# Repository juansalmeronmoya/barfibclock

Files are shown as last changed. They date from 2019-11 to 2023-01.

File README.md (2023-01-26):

IMG_20200908_175020_Bokeh

# BarFIBclock
Repository used to share my work for the clock installed on the [Facultat d'Informàtica de Barcelona (FIB) bar](https://goo.gl/maps/2sY8hWTRuadKxtpD8)

## Materials
 - 28 x 9g Servo [link](https://s.click.aliexpress.com/e/_ABv179)
 - 1 x Arduino Pro mini Atmega328 [link](http://bit.ly/2NVvFll)
 - 2 x I2C PCA9685 servo controller [link](https://s.click.aliexpress.com/e/_AAJpyf)
 - 1 x DC 5V3A adapter [link](http://bit.ly/2NvYGVG)
 - 1 x DC connector [link](http://bit.ly/33AKoJ4)
 - 1 x DS3231 RTC module [link](http://bit.ly/32uphGY)
 - 1 x CR2032 3v battery [link](http://bit.ly/2PYQaAa)
 - 3 x 12mm Metal Push Button Switch Momentary High [link](https://bit.ly/337vpaj)
 - 20 x 150~300mm Servo Extension Lead Wire Cable [link](https://bit.ly/3iaA7dB)
 - 1 x Breadboard Jumper Cable Wires Kit 6cm [link](https://bit.ly/2ZxfuBp)
 - 1 x Red/Black Cable 26AWG 150mm  [link](https://bit.ly/35eJe9F)
 - 12 x M2.5 Screws and nuts
 
### Extras
 - 1 x FTDI USB to TTL UART FT232 [link](https://bit.ly/2R5Vjpw)
 - Cable ties [link](https://s.click.aliexpress.com/e/_9ybz9t)
 - Cyanoacrylate Glue (Superglue like)
 - Heat-shrink tubing [link](https://s.click.aliexpress.com/e/_Aswi55)

## Printing 3D models



| Qty | Filename 
| --- | ---
| 4 | [dc_segment_a.stl](3dparts/frame_segments/dc_segment_a.stl) 
| 4 | [dc_segment_b.stl](3dparts/frame_segments/dc_segment_b.stl) 
| 4 | [dc_segment_c.stl](3dparts/frame_segments/dc_segment_c.stl) 
| 4 | [dc_segment_d.stl](3dparts/frame_segments/dc_segment_d.stl) 
| 4 | [dc_segment_e.stl](3dparts/frame_segments/dc_segment_e.stl) 
| 4 | [dc_segment_f.stl](3dparts/frame_segments/dc_segment_f.stl) 
| 4 | [dc_segment_g.stl](3dparts/frame_segments/dc_segment_g.stl) 
| 4 | [custom_base.stl](3dparts/frame_segments/custom_base.stl) 
| 1 | [dc_base_center.stl](3dparts/frame_segments/dc_base_center.stl) 
| 2 | [dc_frame_corner1.stl](3dparts/frame_segments/dc_frame_corner1.stl) 
| 2 | [dc_frame_corner2.stl](3dparts/frame_segments/dc_frame_corner1.stl) 
| 1 | [dc_frame_top.stl](3dparts/frame_segments/dc_frame_top.stl) 
| 1 | [dc_frame_bottom.stl](3dparts/frame_segments/dc_frame_bottom.stl) 
| 18  | [dc_washer.stl](3dparts/frame_segments/dc_washer.stl)
| 8 | [custom_shoe_ag.stl](3dparts/frame_segments/custom_shoe_ag.stl) 
| 8 | [custom_shoe_bf.stl](3dparts/frame_segments/custom_shoe_bf.stl) 
| 8 | [custom_shoe_ce.stl](3dparts/frame_segments/custom_shoe_ce.stl) 
| 4 | [custom_shoe_d.stl](3dparts/frame_segments/custom_shoe_d.stl)
| 2 | [dc_shoe_center.stl](3dparts/frame_segments/dc_shoe_center.stl)
| 1 | [custom_electronics_case_v2](3dparts/frame_segments/custom_electronics_case_v2.stl)

note: info extracted from http://www.otvinta.com/download14.html

## Electronics


IMG_20211107_132942_Bokeh

## How to program it

Using a USB FTDI controller you can flash the arduino pro mini using arduino IDE selecting this parameters:
* Board: "Arduino Pro or Pro mini"
* Processor: ATmega328P 5V
* Port: your USB FTDI serial port

The programmer is connected with this connection diagram:



## History and Maintenance Book

[Jan 2023] 
* Servos replacement (caused by +800k cycles operation wear) some were died other just as prevention.
* Flashed new servo operation limits

[Dec 2021] 
* Fixed segment movement order and timing to avoid segment collisions
* Upgraded to tighter segment shoes to avoid segment collisions
* Died servos replacement (caused by collisions)

[~2021]
* Died servos replacement (caused by collisions)
* Glued again some servos

[Sept 2020]
* Final hardware with top case and easy programming buttons and wiring
* Installation on the Bar FIB wall, Hurra!

[Dec 2019]
* Hardware and software development with arduino

## Previous work
This project is inspired and based on the otvinta3d clock.
Most of the 3D models used are the same, you can check them out at
https://www.thingiverse.com/thing:3266949

Arduino code are also inspired on the work of https://github.com/ardenpm/servo_clock and https://www.thingiverse.com/thing:3375870

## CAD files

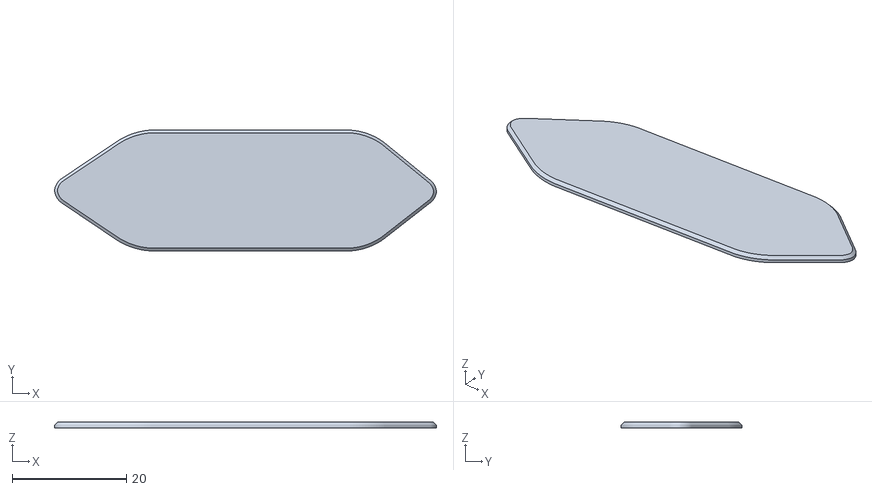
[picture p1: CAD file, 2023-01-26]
3dparts/frame_segments/custom_shoe_d_v2.stl
67.0 x 21.2 x 1.00

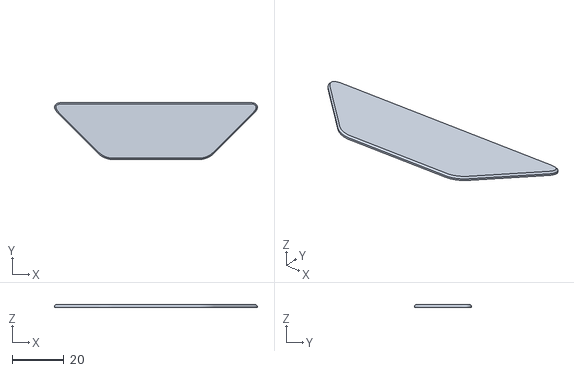
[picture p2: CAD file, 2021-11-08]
3dparts/frame_segments/custom_shoe_ag.stl
78.3 x 22.0 x 1.00

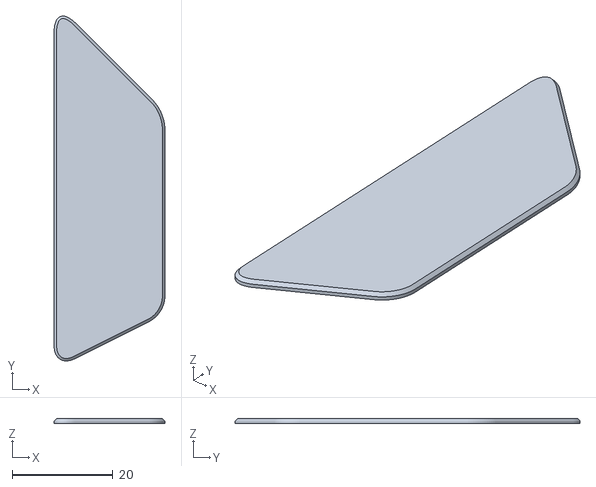
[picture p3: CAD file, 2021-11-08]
3dparts/frame_segments/custom_shoe_bf.stl
22.0 x 68.5 x 1.00

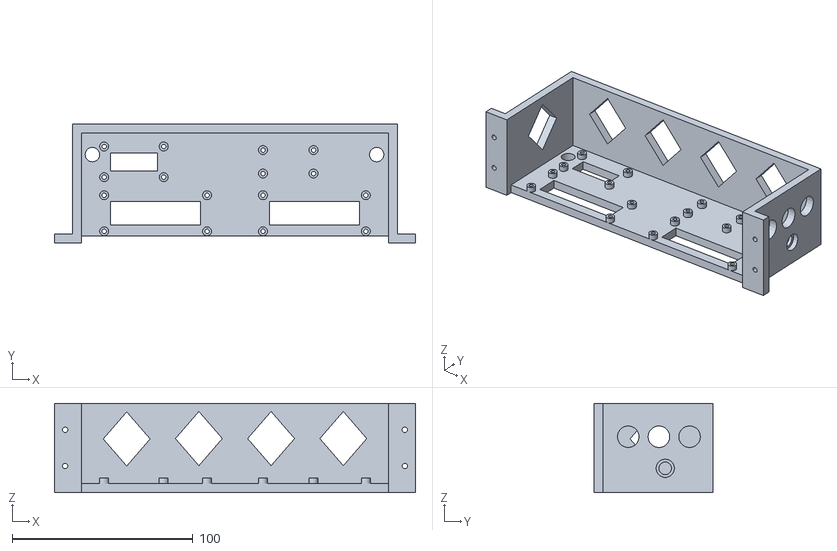
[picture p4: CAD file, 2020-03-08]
3dparts/frame_segments/custom_electronics_case_v2.stl
200.0 x 66.0 x 49.5

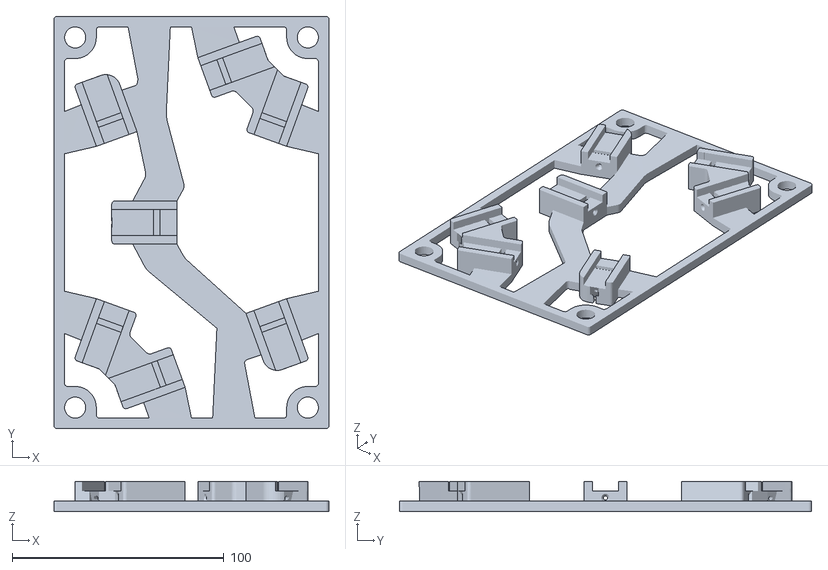
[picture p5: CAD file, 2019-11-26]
3dparts/frame_segments/custom_base.stl
130.0 x 195.0 x 14.3

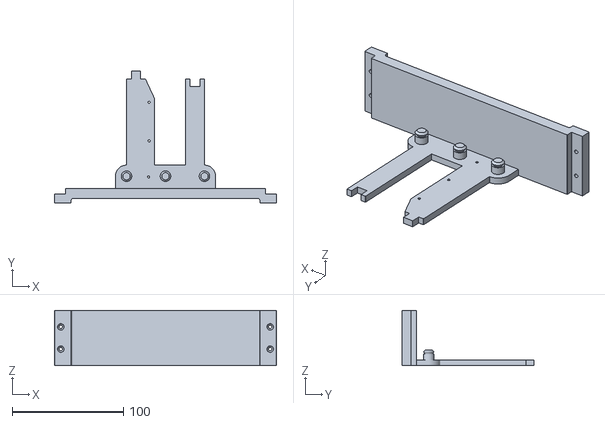
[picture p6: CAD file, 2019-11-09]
3dparts/frame_segments/dc_frame_bottom.stl
199.5 x 118.5 x 49.6

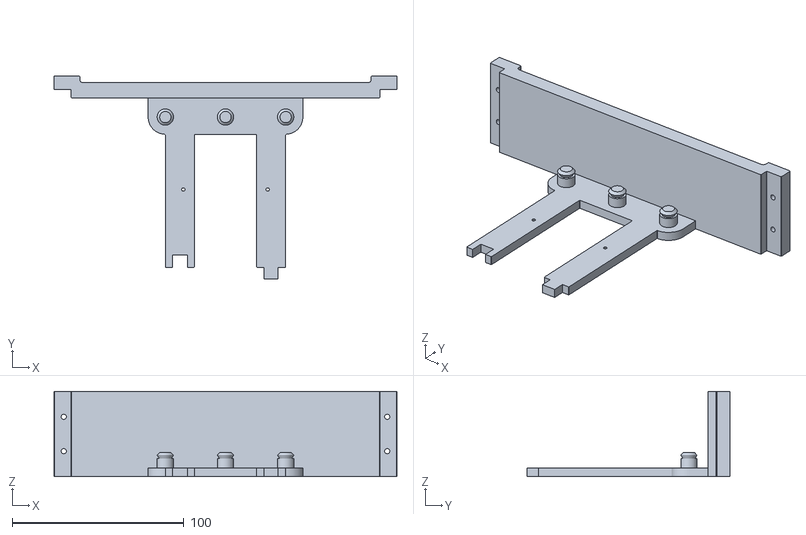
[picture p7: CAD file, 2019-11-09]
3dparts/frame_segments/dc_frame_top.stl
199.5 x 118.3 x 49.6

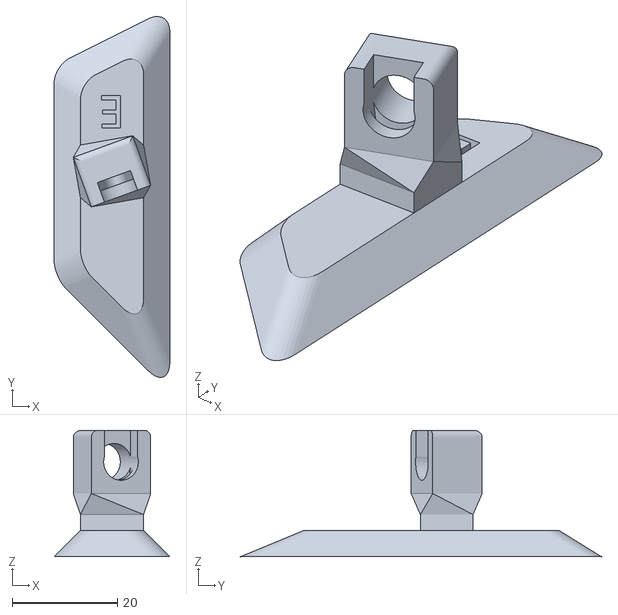
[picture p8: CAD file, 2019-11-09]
3dparts/frame_segments/dc_segment_e.stl
22.0 x 68.5 x 24.0

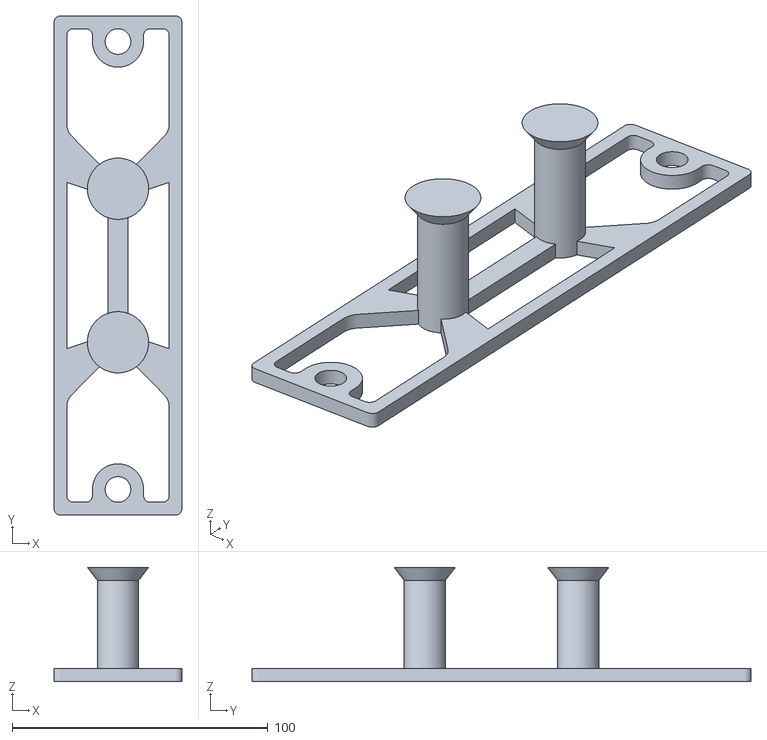
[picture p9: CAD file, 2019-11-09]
3dparts/frame_segments/dc_base_center.stl
50.0 x 195.0 x 44.6

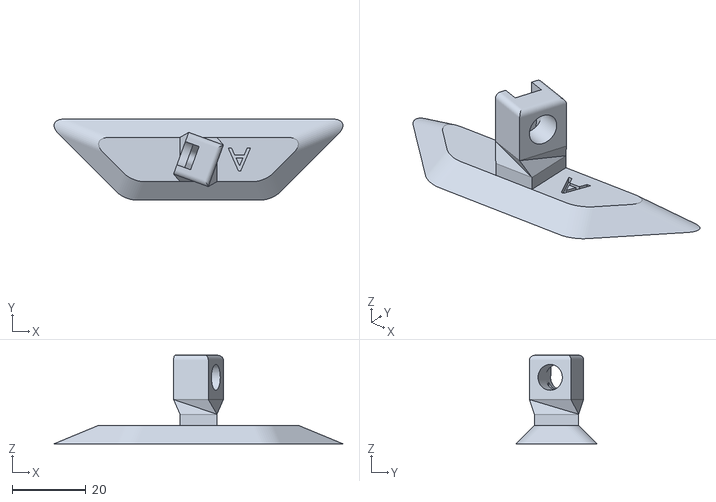
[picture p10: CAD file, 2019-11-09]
3dparts/frame_segments/dc_segment_a.stl
78.3 x 22.0 x 24.0

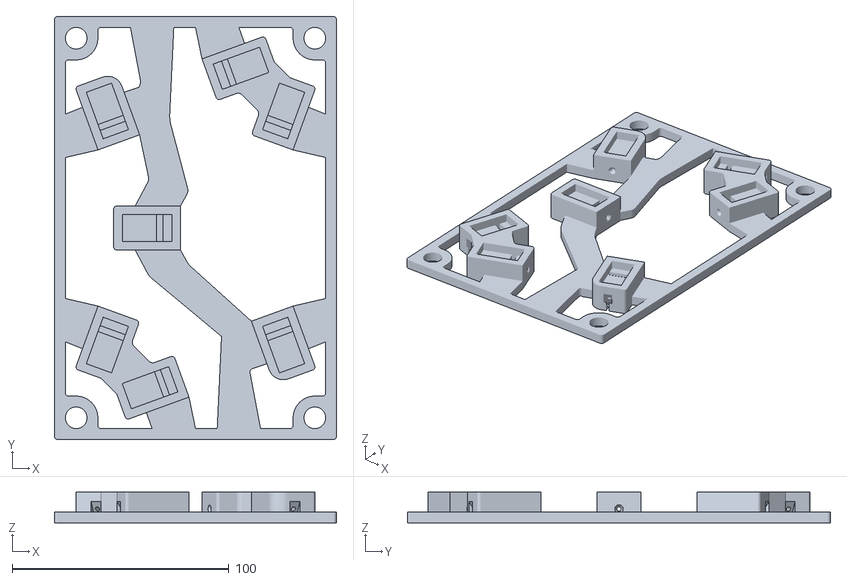
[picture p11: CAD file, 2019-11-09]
3dparts/frame_segments/dc_base.stl
130.0 x 195.0 x 14.3

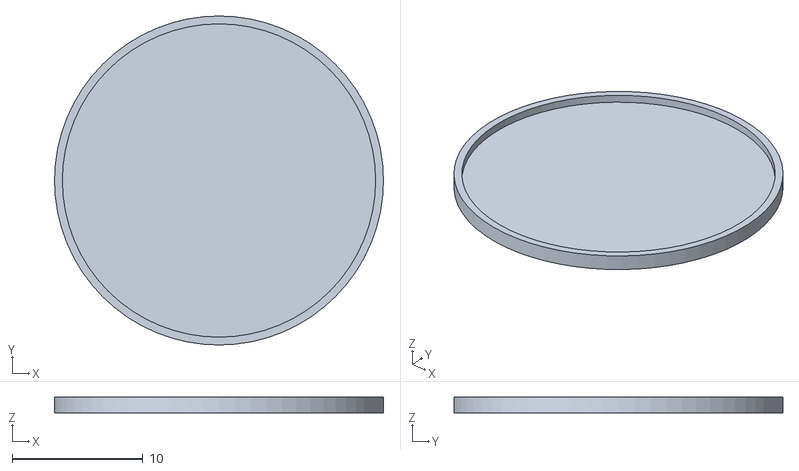
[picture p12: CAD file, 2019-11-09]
3dparts/frame_segments/dc_shoe_center.stl
25.1 x 25.1 x 1.20

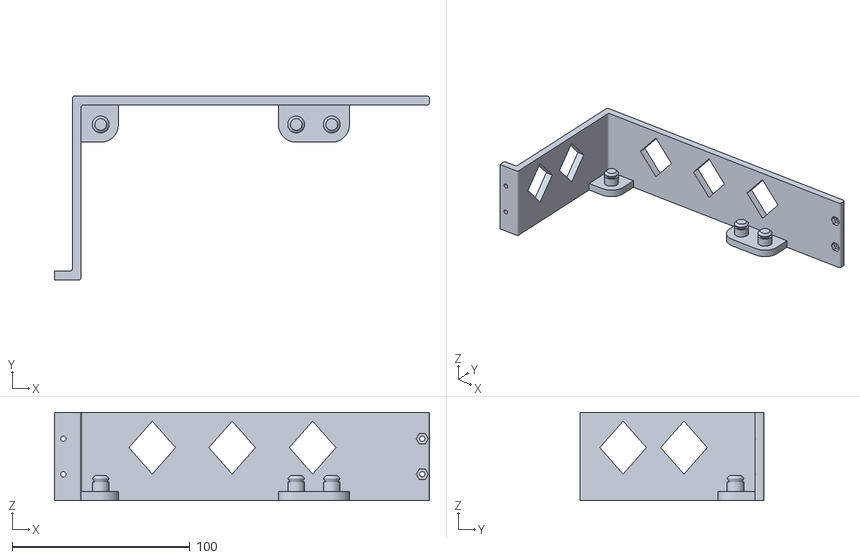
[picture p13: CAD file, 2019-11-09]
3dparts/frame_segments/dc_frame_corner1.stl
211.0 x 103.5 x 49.6

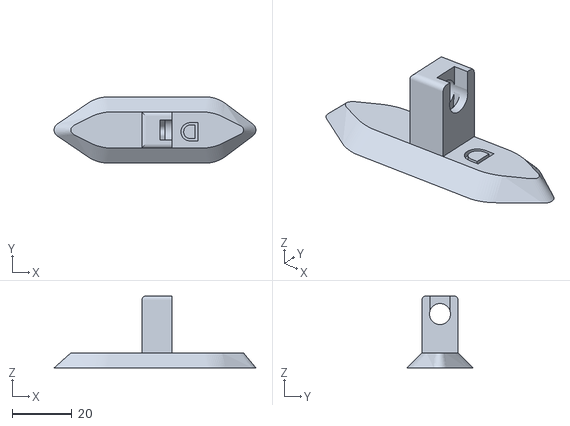
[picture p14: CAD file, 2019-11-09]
3dparts/frame_segments/dc_segment_d.stl
67.4 x 22.0 x 24.0

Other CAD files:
3dparts/frame_segments/custom_shoe_ce.stl
3dparts/frame_segments/dc_segment_c.stl
3dparts/frame_segments/dc_segment_b.stl
3dparts/frame_segments/dc_segment_g.stl
3dparts/frame_segments/custom_shoe_d.stl
3dparts/frame_segments/dc_frame_corner2.stl
3dparts/frame_segments/dc_segment_f.stl
3dparts/frame_segments/dc_washer.stl

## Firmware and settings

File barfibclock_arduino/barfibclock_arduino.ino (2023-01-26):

#include <Wire.h>
#include <Adafruit_PWMServoDriver.h> // PCA9685 library
#include <RTClib.h> //Real Time Clock library

Adafruit_PWMServoDriver servoHours = Adafruit_PWMServoDriver(0x40); //first PCA9685 address
Adafruit_PWMServoDriver servoMinutes = Adafruit_PWMServoDriver(0x41); //second PCA9685 address
RTC_DS3231 rtc; //RTC address

// reference LOW to power buttons
const int setmodelow_pin = 4;
const int setpluslow_pin = 6;
const int setminuslow_pin = 2;

// servo enable pin
const int enablepin = 12;

// read button pins
const int setmodepin = 5;
const int setpluspin = 7;
const int setminuspin = 3;

const byte mapchar [11][7] = { //for each number, position of every segment
  {1, 1, 1, 0, 1, 1, 1}, // zero - segment number from top lo low, left to right
  {0, 0, 1, 0, 0, 1, 0}, // one
  {1, 0, 1, 1, 1, 0, 1}, // two
  {1, 0, 1, 1, 0, 1, 1}, // three
  {0, 1, 1, 1, 0, 1, 0}, // four
  {1, 1, 0, 1, 0, 1, 1}, // five
  {1, 1, 0, 1, 1, 1, 1}, // six
  {1, 0, 1, 0, 0, 1, 0}, // seven
  {1, 1, 1, 1, 1, 1, 1}, // eight
  {1, 1, 1, 1, 0, 1, 1}, // nine
  {0, 0, 0, 0, 0, 0, 0} // null (all down)
};

const int servolow [4] [7] = { 
// pulse to add to servopulse for fine tunning of each individual servo
// higher numbers represents a servo position more clockwise if you look the servo from the cable side
  {400, 500, 130, 180, 280, 410, 330}, //digit 0. 
  {420, 330, 170, 180, 180, 400, 350}, //digit 1
  {400, 400, 210, 180, 270, 510, 380}, //digit 2
  {390, 420, 250, 210, 250, 460, 370}  //digit 3
};

const int servohigh [4] [7] = { 
// pulse to add to servopulse for fine tunning of each individual servo
// higher numbers represents a servo position more clockwise if you look the servo from the cable side
  {220, 300, 380, 410, 480, 170, 130}, //digit 0 
  {220, 130, 410, 400, 420, 130, 170}, //digit 1 
  {190, 180, 480, 400, 510, 270, 180}, //digit 2
  {200, 190, 450, 450, 440, 230, 170}  //digit 3
};

byte moment [4] = {8, 8, 8, 8}; // actual time
byte momentnull [4] = {10, 10, 10, 10}; // all digits in null for startup
byte momenthigh [4] = {8, 8, 8, 8}; // all digits in null for startup
byte momentdisplay [4]; //time shown in display

void setup() {

  Serial.begin(9600);
  rtc.begin();
  //rtc.adjust(DateTime(__DATE__, __TIME__)); //uncomment to set time to now
  //rtc.adjust(DateTime(2019, 12, 27, 22, 51, 0)); 
  pinMode(enablepin, OUTPUT); // this is the pin for OE in the PCA (enable/disable servos LOW/HIGH)
  pinMode(setmodelow_pin, OUTPUT);
  pinMode(setpluslow_pin, OUTPUT);
  pinMode(setminuslow_pin, OUTPUT);
  digitalWrite(setmodelow_pin, LOW);
  digitalWrite(setpluslow_pin, LOW);
  digitalWrite(setminuslow_pin, LOW);
  pinMode(setmodepin, INPUT_PULLUP); // this is the pin for set time button
  pinMode(setpluspin, INPUT_PULLUP); // this is the pin for set plus button
  pinMode(setminuspin, INPUT_PULLUP); // this is the pin for set minus button
  servoHours.begin();
  servoHours.setPWMFreq(50); // set frequncy for first PCA
  servoMinutes.begin();
  servoMinutes.setPWMFreq(50); // set frequency for second PCA
  showtime(moment, 0);
  showtime(momentnull, 50);
}

void loop() {
  //tuning();
  capturetime(); // captura el momento!
  showtime(moment, 20);
  while (momentdisplay[3] == moment[3]) { // wait while minutes doesnt change...
    if (digitalRead(setmodepin) != HIGH) setmode(momentdisplay);
    capturetime();
  }
}

void tuning() {
  byte servoToTune = 0;
  int pulseToTune = 0;
  
  while (!Serial) {
    ; // wait for serial port to connect. Needed for native USB
  }
  if (Serial.available() > 0) {
    Serial.println("Enter servo to tune");
    servoToTune = Serial.readString().toInt();

    Serial.print("Tuning servo #");
    Serial.println(servoToTune, DEC);
    

    while (pulseToTune != -1) {
      if (Serial.available() > 0) {
        Serial.println("Enter pulse to test, -1 for exit"); 
        pulseToTune = Serial.readString().toInt();
        
        Serial.print("Servo #");
        Serial.print(servoToTune, DEC);
        Serial.print(" value: ");
        Serial.println(pulseToTune, DEC);

        //move servo
        digitalWrite(enablepin, LOW);
        if(servoToTune >= 21) {
          servoMinutes.setPWM(servoToTune-13, 0, pulseToTune);
        } else if(servoToTune >= 14 && servoToTune < 21) {
          servoMinutes.setPWM(servoToTune-14, 0, pulseToTune);
        } else if(servoToTune >= 7 && servoToTune < 14) {
          servoHours.setPWM(servoToTune+1, 0, pulseToTune);
        } else{
          servoHours.setPWM(servoToTune, 0, pulseToTune);
        }
        delay(1000);
        digitalWrite(enablepin, HIGH);
      }
    }
    pulseToTune = 0;
  }
}

void capturetime() {
  DateTime now = rtc.now(); // save in variable now the actual time;
  moment[0] = now.hour() / 10; // find out first digit from hour
  moment[1] = now.hour() - moment[0] * 10; // find out second digit from hour
  moment[2] = now.minute() / 10; // find our first digit from minute
  moment[3] = now.minute() - moment[2] * 10; // find out second digit from minute
}

void showtime(byte m [4], int w) {
  int d = 1200; // delay needed to stop the servos moving before disabling them
  // parameters: matrix with the digits to show
  if (memcmp(m, momentdisplay, 4) != 0) { // if time displayed is different to time expected to be shown
    digitalWrite(enablepin, LOW); // enable the servos
    for (int i = 0; i < 4; i++) { // for every single position, show only if different to actually shown
      if (m[i] != momentdisplay[i]) {
        showdigit(i, m[i], w);
        momentdisplay [i] = m[i]; // take note of the shown digit
      }
    }
    delay(d); // give time to the servos to stop moving before disabling them
    digitalWrite(enablepin, HIGH); // disable the servos
  }
}

void moveSegment(byte digitNumber, byte digitPosition, byte segmentNumber, int delayMs) {
  // parameters: 
  //
  // digitNumber = [0,1,2,3,4,5,6,7,8,9] is the number we want to show using the segments
  // digitPosition = [0,1,2,3] is the position of the number we want to show on the clock starting from the left side. 01:23 
  // segmentNumber = [0,1,2,3,4,5,6] the segment of the digit we sant to move. See the layout used on the README.md
  // delayMS = amount of time between segment moves in milliseconds.
  //
  int pulse;
  byte servonum, a, segmentposition;
  
  servonum = segmentNumber + (8 * ((digitPosition == 1 || digitPosition == 3))); // add 8 if position is 1 or 3 because 1 ands 3 digits start on pin 8 of the PCA
  segmentposition = mapchar[digitNumber] [segmentNumber]; // segment should be low or high?
  if (segmentposition == 0) {
    pulse = servolow[digitPosition][segmentNumber];
  } else {
    pulse = servohigh[digitPosition][segmentNumber];
  }

  switch (digitPosition) { // switch for both PCA controllers
    case 0: case 1:
      servoHours.setPWM(servonum, 0, pulse);
      break;
    case 2: case 3:
      servoMinutes.setPWM(servonum, 0, pulse);
      break;
  }
  delay(delayMs); // delay in between movement of contiguous segments, so we can do waves oleeeeeeee. Normally is 0.
}

void showdigit(byte digitPosition, byte digitNumber, int delayMs) {
  // parameters: digit position =01:23, digit to show

  // first we are ging to move down upper side segments (1 and 2) to avoid collision with central segment (3)
  moveSegment(10,digitPosition,1,delayMs);
  moveSegment(10,digitPosition,2,delayMs);

  // move the 7 segment on specific order to avoid collisions
  moveSegment(digitNumber,digitPosition,0,delayMs);
  moveSegment(digitNumber,digitPosition,6,delayMs);
  delay(100);
  moveSegment(digitNumber,digitPosition,3,delayMs);
  moveSegment(digitNumber,digitPosition,4,delayMs);
  moveSegment(digitNumber,digitPosition,5,delayMs);
  delay(100);
  moveSegment(digitNumber,digitPosition,1,delayMs);
  moveSegment(digitNumber,digitPosition,2,delayMs);
}

void setmode(byte m[4]) {
  // parameter is the moment in display and the one we will set and finally save in the RTC
  int hourset = m[0] * 10 + m[1];
  int minuteset = m[2] * 10 + m[3];
  byte mset[4];
  int d = 200; // delay on button press

  // set hours
  mset[0] = m[0]; //mset is the array to show while setting time
  mset[1] = m[1];
  mset[2] = 10; // we start setting hours, so let's show minutes blank
  mset[3] = 10;
  showtime(mset, 0);
  delay(d); // the delays in this routine are the wait between button press

  while (digitalRead(setmodepin) == HIGH) { // wait in set hour mode until we press again the set button
    if (digitalRead(setpluspin) != HIGH) {
      hourset = (hourset + 1) % 24; // add one hour and do modulo 24
      mset[0] = hourset / 10; // assign to mset in order to be displayed
      mset[1] = hourset - mset[0] * 10;
      showtime(mset, 0); // display the set time
      delay(d);
    }
    if (digitalRead(setminuspin) != HIGH) {
      hourset = (hourset - 1); // substract one to hour and if neative assign 23 (next line)
      if (hourset < 0) hourset = 23;
      mset[0] = hourset / 10;
      mset[1] = hourset - mset[0] * 10;
      showtime(mset, 0);
      delay(d);
    }
  }

  // set minutes
  mset[0] = 10; //let's start setting minutes, so show blank hours
  mset[1] = 10;
  mset[2] = minuteset / 10;
  mset[3] = minuteset - mset[2] * 10;
  showtime(mset, 0);
  delay(d);
  while (digitalRead(setmodepin) == HIGH) { //setting minutes until we press again the set button
    if (digitalRead(setpluspin) != HIGH) {
      minuteset = (minuteset + 1) % 60; // same math as previously done to hours
      mset[2] = minuteset / 10;
      mset[3] = minuteset - mset[2] * 10;
      showtime(mset, 0);
      delay(d);
    }
    if (digitalRead(setminuspin) != HIGH) {
      minuteset = (minuteset - 1);
      if (minuteset < 0) minuteset = 59;
      mset[2] = minuteset / 10;
      mset[3] = minuteset - mset[2] * 10;
      showtime(mset, 0);
      delay(d);
    }
  }
  rtc.adjust(DateTime(2019, 1, 16, hourset, minuteset, 0)); //save time in RTC, date is useless so let's invent it
  capturetime(); // capturte the time in variable moment (is reduntant, but just to make sure jeje)
  showtime(moment, 0); // show the actual time
  delay(d * 2);
}

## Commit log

2019-11-09 Import 3d models from Otvinta thingiverse repo
    [dc_base.stl, dc_base_center.stl, dc_frame_bottom.stl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]
2019-11-10 Update material list
2019-11-10 Update materials
2019-11-26 Add custom base frame for chinese servo replicas
    [dc_base_custom.stl]
2019-12-19 Calibrate digit 0
    [configuration.h]
2019-12-20 Refactor to use different arrays for low and high servo positions
2019-12-27 Add tuning and set high and low values for servos
2019-12-27 Remove servoreverse control
2019-12-28 Print time twice to avoid an unknown bug
    [barfibclock_arduino.ino]
2020-02-21 Add electronics case
    [electronics_case_v1.stl]
2020-02-21 Disabled low power consumption
2020-03-08 Make bigger button holes in electronic case
    [electronics_case_v2.stl]
2020-09-07 Add pins for programming buttons
2021-11-04 Add more materials
2021-11-04 Remove unused files
    [configuration.h]
2021-11-08 Add new custom slim "shoes"
    [custom_base.stl, custom_electronics_case_v2.stl, custom_shoe_ag.stl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]
2021-11-08 Add d segment shoe
    [dc_shoe_d.stl]
2021-12-10 Fix collision issue with central segment
    [barfibclock_arduino.ino]
2023-01-26 Fix with new servo low and high limits
    [custom_shoe_d_v2.stl]
